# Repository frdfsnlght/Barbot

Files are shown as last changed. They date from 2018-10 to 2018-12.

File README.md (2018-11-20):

# Barbot
My Barbot project

This repository stores all the design artifacts for the project and is freely
available to anyone who wants to learn about my project.

## Why?

There are hundreds, if not thousands, of barbots made by makers all over the world.
It might be a right of passage for some, but for me, it was an interesting idea that
gave me an excuse to learn some new things.

I had the idea to build one of these things years ago with a friend. The main detraction
for me was that most barbot build I've seen are either too large or too slow, in my
opinion. If I was going to build one of these, it had to be small and convenient
enough to easily store when not in use, easy to clean after being used, and it couldn't
take forever to dispense a drink.
Those requirements are completely subjective but I eventually came up
with some numbers that would satisfy me. My goals were to be able to store the device
on an existing shelf in a spare room in my house and it had to be able to make me a
drink (e.g., a rum and coke) in under 10 seconds. The cleaning aspect is more difficult
to quantify but I didn't want to have to disassemble the device or do anything else
drastic to get it cleaned up.

## How?

In the spring of 2018 I revisited the idea of building a barbot when I found some
published builds using peristaltic pumps. I had never considered individual pumps
for each ingredient, but doing so solved some of the problems I felt other designs
suffered from. After investigating, I discovered peristaltic pumps generally come
in two forms, small and slow, or large and expensive. Neither was satisfactory, so
I started  considering making my own pumps. This eventually led to 3D printing,
something I had never really had a need of before. I started designing a
pump that could meet my needs and eventually bought a 3D printer and started
building a prototype. After a few iterations and lots of fiddling around, I came
up with a design that worked. You can find out more about the pump [here](3D).

Once I had the pump designed and tested, the possibility of building a complete
barbot became real. All I would need to do was the rest of the design and build.

## More to come...

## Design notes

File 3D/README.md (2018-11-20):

# 3D

These are SketchUp Make 2017 files for the most part.

## Enclosure

This file contains the model for the entire enclosure and most of the internal parts, except for the
pumps. Printable parts have been exported as STL to the STLs directory.

## Pump

This file contains all the parts for the planetary gear, peristaltic pump I designed. Every part except
the stepper motor can be printed and all parts have been exported to the STLs directory.

## Print Settings

All these parts were sliced with Slic3r Prusa Edition for an Original Prusa MK3 with a layer height of 0.15mm.

File            | Part                                                          | Material  | Infill            | Perimeters| Top/Bot   | Quantity
---             | ---                                                           | ---       | ---               | ---       | ---       | ---
Enclosure       | [Dispenser Head Part A](STLs/Dispenser%20Head%20Part%20A.stl) | PLA       | 40% Grid          | 2         | 7/5       | 1
Enclosure       | [Dispenser Head Part B](STLs/Dispenser%20Head%20Part%20B.stl) | PLA       | 20% Grid          | 2         | 7/5       | 1
Enclosure       | [Dispenser Head Part C](STLs/Dispenser%20Head%20Part%20C.stl) | PLA       | 40% Grid          | 2         | 7/5       | 1
Enclosure       | [Dispenser Head Part D](STLs/Dispenser%20Head%20Part%20D.stl) | PETG      | 40% Grid          | 2         | 7/5       | 1
Enclosure       | [Raspberry Pi Offset Bracket](STLs/Raspberry%20Pi%20Offset%20Bracket.stl) | PLA      | 20% Grid     | 2         | 7/5       | 4
Enclosure       | [Touch Screen Bracket](STLs/Touchscreen%20Bracket.stl)        | PETG      | 50% Grid          | 2         | 7/5       | 2
Enclosure       | [Drip Tray](STLs/Drip%20Tray.stl)                             | PETG      | 20% Grid          | 2         | 7/5       | 1
Enclosure       | [Drip Tray Cover](STLs/Drip%20Tray%20Cover.stl)               | PETG      | 15% Honeycomb     | 10        | 0/0       | 1
Enclosure       | [Speaker Grill](STLs/Speaker%20Grill.stl)                     | PETG      | 20% Honeycomb     | 8         | 0/0       | 2
Enclosure       | [Fan Grill](STLs/Fan%20Grill.stl)                             | PETG      | 15% Honeycomb     | 14        | 0/0       | 1
Enclosure       | [Tubing Bender](STLs/Tubing%20Bender.stl)                     | PETG      | 20% Grid          | 5         | 7/5       | 2
Pump            | [Sun Gear](STLs/Sun%20Gear.stl)                               | PLA       | 100% Rectilinear  | 5         | 7/5       | 32
Pump            | [Sun Roller](STLs/Sun%20Roller.stl)                           | PLA       | 50% Grid          | 5         | 7/5       | 16
Pump            | [Planet Gear](STLs/Planet%20Gear.stl)                         | PLA       | 100% Rectilinear  | 5         | 7/5       | 64
Pump            | [Planet Roller](STLs/Planet%20Roller.stl)                     | PLA       | 50% Grid          | 5         | 7/5       | 32
Pump            | [Clamp Block Left](STLs/Clamp%20Block%20Left.stl)             | PLA       | 20% Grid          | 2         | 7/5       | 16
Pump            | [Clamp Block Right](STLs/Clamp%20Block%20Right.stl)           | PLA       | 20% Grid          | 2         | 7/5       | 16
Pump            | [Motor Plate](STLs/Motor%20Plate.stl)                         | PLA       | 20% Grid          | 2         | 7/5       | 16
Pump            | [Ring Plate A](STLs/Ring%20Plate%20A.stl)                     | PLA       | 50% Grid          | 5         | 7/5       | 16
Pump            | [Ring Plate B](STLs/Ring%20Plate%20B.stl)                     | PLA       | 50% Grid          | 5         | 7/5       | 16
Pump            | [Body Plate A](STLs/Body%20Plate%20A.stl)                     | PLA       | 50% Grid          | 5         | 7/5       | 16
Pump            | [Body Plate B](STLs/Body%20Plate%20B.stl)                     | PLA       | 50% Grid          | 5         | 7/5       | 16

## Bill of Materials

This is a mostly complete list of every conceivable off-the-shelf part that will be required. You can find everything online,
but some of it can be found at a local, well stocked hardware store.
I've included links and approximate pricing where I could. Some of the online quantities are way more than you'll need.

### Hardware

Each item is linked to a McMaster-Carr product page and lists a price as of November 2018. I actually purchased much of this
from my local hardware store, but the larger quantity items were bought online. I've also substituted some hardware for other
pieces because I couldn't get some of the small quantities locally. For instance, rather than use 2.5mm screws to attach the
*Touchscreen Offset Bracket* to the back of the touchscreen, I tapped those holes to 3mm and used the same screws I used to
attach the Pi to the bracket. Use your best judgment.

Description                                                                                 | Quantity | Price
---                                                                                         | ---      | ---
[#8 x <sup>5</sup>/<sub>8</sub>" SS Phillips Oval Head Metal Screws](https://www.mcmaster.com/90315A467)          | 100 | $6.03
 *Side Panels*                                                                              |  16
 *Dispenser Panels*                                                                         |  16
 *Back*                                                                                     |   6
 *Controller*                                                                               |  14
 *Top Panel Brackets*                                                                       |   8
 *Pump Holder Brackets*                                                                     |   8
 *PCB Panel Brackets*                                                                       |   4
 *Power Supply Panel*                                                                       |   2
 *Relay Panel*                                                                              |   2
[#8 x 1" SS Phillips Round Head Metal Screws](https://www.mcmaster.com/92470A199)           | 100 | $8.13
 *LED Panel*                                                                                |   2
[#8 x <sup>5</sup>/<sub>8</sub>" SS Phillips Flat Head Metal Screws](https://www.mcmaster.com/90065A195)          | 100 | $5.50
 *Dispenser Panels*                                                                         |   2
 *Front*                                                                                    |   2
 *Pumps*                                                                                    |  32
 *Hinge Supports*                                                                           |   4
[#6 x <sup>5</sup>/<sub>8</sub>" SS Phillips Flat Head Metal Screws](https://www.mcmaster.com/90065A149)          | 100 | $3.89
 *Controller*                                                                               |   1
 *Hinges*                                                                                   |   4
[#6 x <sup>3</sup>/<sub>8</sub>" SS Phillips Flat Head Machine Screws](https://www.mcmaster.com/91771A146)        | 100 | $5.13
 *Hinges*                                                                                   |   4
[#4-40 x 5/8" Steel Phillips Flat Head Machine Screws](https://www.mcmaster.com/90273A112)  | 100 | $2.74
 *PCB Panel*                                                                                |  14
 *Relay Panel*                                                                              |   8
[#4-40 Steel Hex Nuts](https://www.mcmaster.com/90480A005)                                  | 100 | $0.89
 *PCB Panel*                                                                                |  14
 *Relay Panel*                                                                              |   8
[#8 x 1/4" x 1/4" Nylon Spacers](https://www.mcmaster.com/94639A293)                        | 100 | $8.75
 *PCBs*                                                                                     |  14
 *Relays*                                                                                   |   8
 *LED Panel*                                                                                |   4
[4mm x 35mm SS Socket Head Machine Screws](https://www.mcmaster.com/91292A131)              |  50 | $7.08
 *Fan*                                                                                      |   4
[4mm SS Hex Nuts](https://www.mcmaster.com/91828A231)                                       | 100 | $6.45
 *Fan*                                                                                      |   4
[3mm x 25mm SS Socket Head Machine Screws](https://www.mcmaster.com/91292A020)              | 100 | $6.87
 *Dispenser Head*                                                                           |   4
 *Pumps*                                                                                    |  80
[3mm x 20mm SS Socket Head Machine Screws](https://www.mcmaster.com/91292A123)              | 100 | $6.44
 *Dispenser Head*                                                                           |   1
 *Speakers*                                                                                 |   8
[3mm x 10mm SS Hex Drive Flat Head Machine Screws](https://www.mcmaster.com/92125A130)      | 100 | $5.81
 *Power Socket*                                                                             |   2
[3mm x 8mm SS Phillips Pan Head Machine Screws](https://www.mcmaster.com/92000A118)         | 100 | $4.33
 *Touchscreen Bracket*                                                                      |   4
 *PCB Panel*                                                                                |   4
[3mm x 8mm SS Hex Drive Flat Head Machine Screws](https://www.mcmaster.com/92125A128)       | 100 | $3.54
 *Power Supply Panel*                                                                       |   6
 *Pumps*                                                                                    |  64
[3mm x 12mm SS Hex Drive Button Head Machine Screws](https://www.mcmaster.com/92095A183)    | 100 | $4.00
 *Touchscreen Offset Bracket*                                                               |   4
[2.5mm x 12mm SS Hex Drive Button Head Machine Screws](https://www.mcmaster.com/92095A461)  |  25 | $9.57
 *Touchscreen Offset Bracket*                                                               |   4
[3mm SS Hex Nuts](https://www.mcmaster.com/91828A211)                                       | 100 | $5.55
 *Power Socket*                                                                             |   2
 *Pumps*                                                                                    |  80
 *Dispenser Head*                                                                           |   5
 *Speakers*                                                                                 |   8
 *Touchscreen Offset Bracket*                                                               |   4
[3mm SS Slim Hex Nuts](https://www.mcmaster.com/90710A030)                                  | 100 | $6.86
 *Pumps*                                                                                    |  32
[3mm x 5mm SS Flat Tip Set Screws](https://www.mcmaster.com/92605A099)                      |  50 | $5.72
 *Pumps*                                                                                    |  32
[<sup>1</sup>/<sub>8</sub>" x 1 <sup>3</sup>/<sub>8</sub>" OD O-Ring](https://www.mcmaster.com/9452K36)     | 100 | $8.81
 *Dispenser Head*                                                                           |   1
[3/4" x 9/16" Rubber Feet](https://www.mcmaster.com/8884T21)                                |  10 | $5.17
 *Bottom*                                                                                   |   4

### Electronics

Here's a list of all the electrical parts you'll need. Note, you'll also need the circuit boards that also part of this project,
as well as wire, a soldering iron, connectors, etc.

* Raspberry Pi 3 Model B (Amazon)
* 16GB Micro SD Card (Amazon)
* Teensy 3.2 (OSHPark with PCB order)
* Arduino Pro Mini
* Relays (eBay)
* Amplifier (Amazon)
* Speakers (Salvage)
* Stepper Drivers (AliExpress)
* 10 uF Capacitors (AliExpress)
* 1000 uF Capacitor (Amazon)
* Spade Solder Terminals (Amazon)
* Power Socket (eBay)
* Switch (Amazon)
* Stepper Motors (AliExpress)
* 80mm Fan (Salvage)
* IR Sensor (Amazon)
* 5V 12A Power Supply (Amazon)
* 24V 5A Power Supply (eBay)
* LEDs (eBay)
* Power Cord (Surplus)

### Other

Here's a few other important parts that didn't fit well in any other category.

* Funnel (Amazon)
* Hinges (Amazon)
* <sup>1</sup>/<sub>8</sub>" x 2' x 4' Acrylic Sheet, Black (Amazon)
* 4' x 4' x <sup>3</sup>/<sub>4</sub>" Birch Plywood (Surplus)
* Solid Birch Plank (Surplus)
* <sup>3</sup>/<sub>16</sub>" Brake Line (Amazon)
* 8mm/6mm Silicone Tubing (Amazon)
* 6mm/4mm Silicone Tubing (Amazon)

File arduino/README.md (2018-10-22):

# arduino
Firmware for Barbot's Arduino microcontroller.

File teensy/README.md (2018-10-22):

# teensy
Firmware for Barbot's Teensy microcontroller.

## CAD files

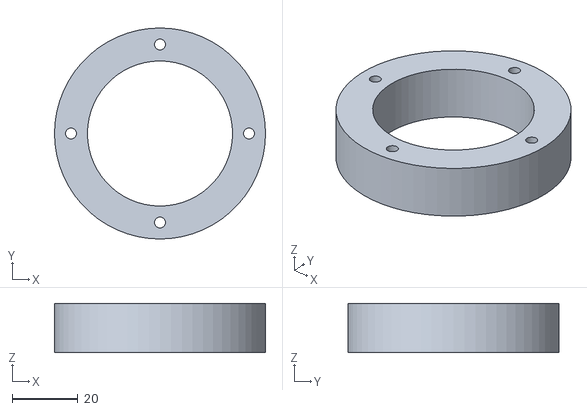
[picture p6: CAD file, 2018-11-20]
3D/STLs/Dispenser Head Part B.stl
64.0 x 64.0 x 15.0

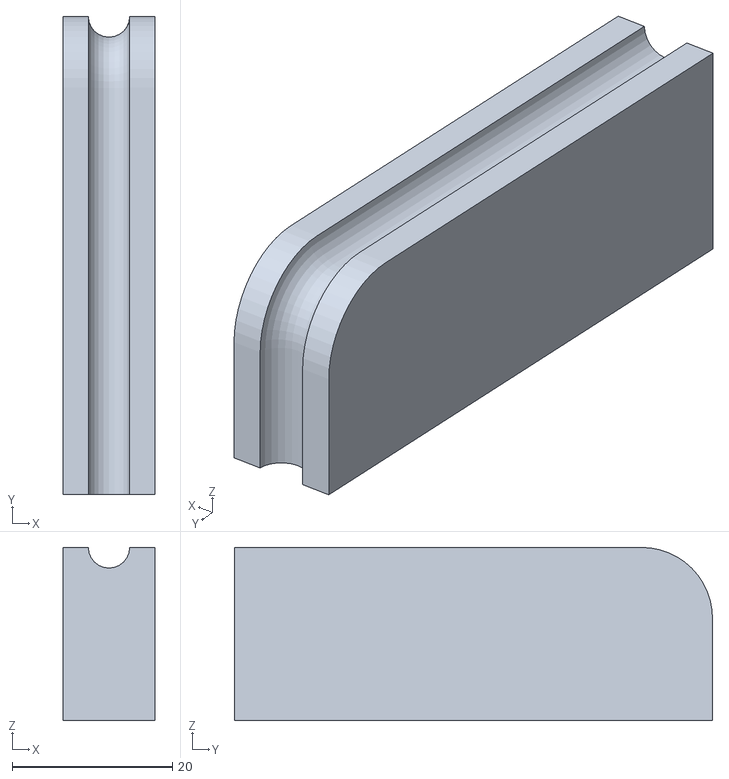
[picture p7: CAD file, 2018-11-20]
3D/STLs/Tubing Bender.stl
11.5 x 59.7 x 21.6

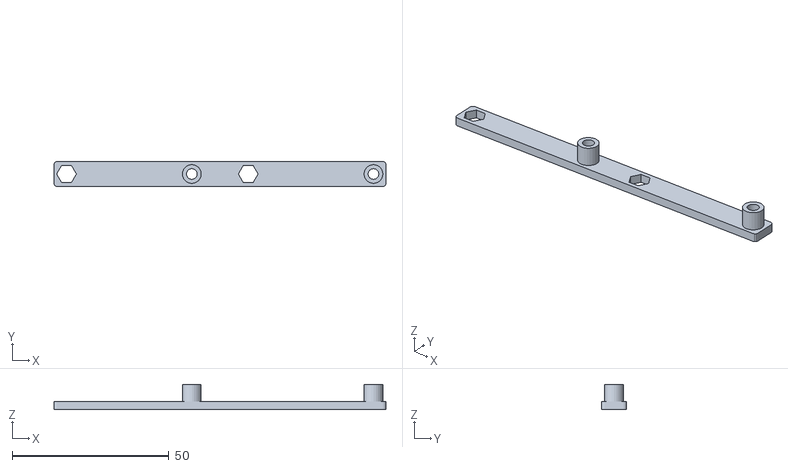
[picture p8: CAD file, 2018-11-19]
3D/STLs/Raspberry Pi Offset Bracket.stl
106.0 x 8.00 x 8.00

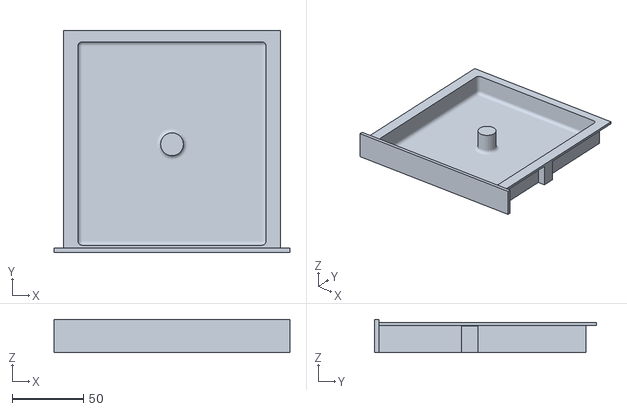
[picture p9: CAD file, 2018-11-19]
3D/STLs/Drip Tray.stl
165.1 x 155.2 x 23.3

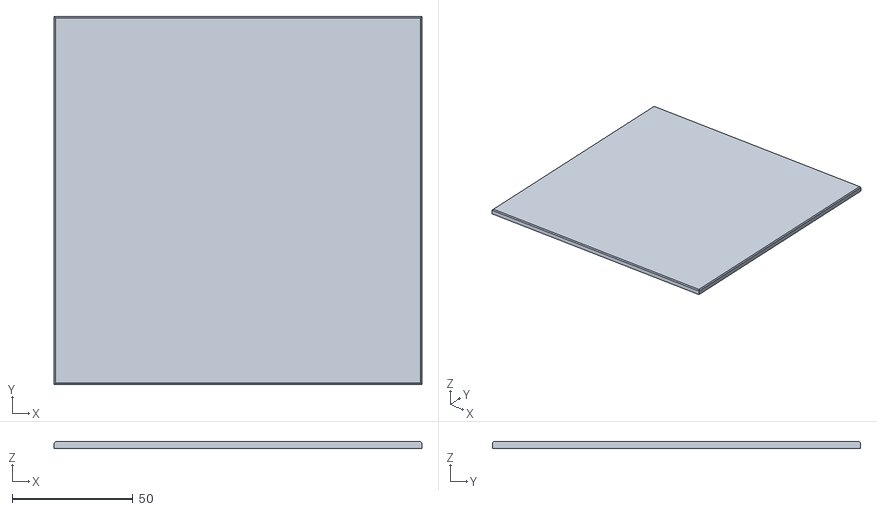
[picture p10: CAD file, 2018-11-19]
3D/STLs/Drip Tray Cover.stl
152.0 x 152.2 x 3.00

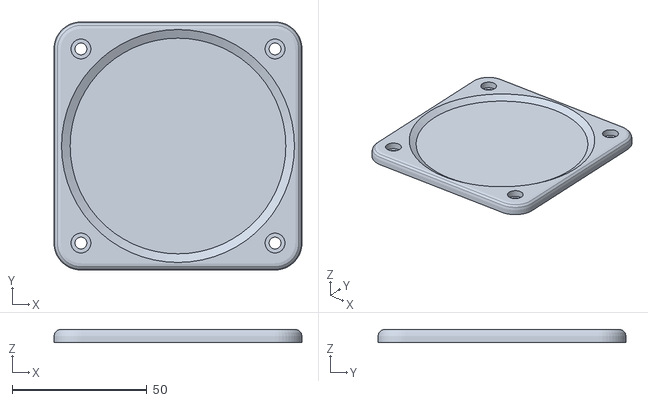
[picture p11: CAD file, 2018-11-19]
3D/STLs/Fan Grill.stl
92.0 x 92.0 x 5.00

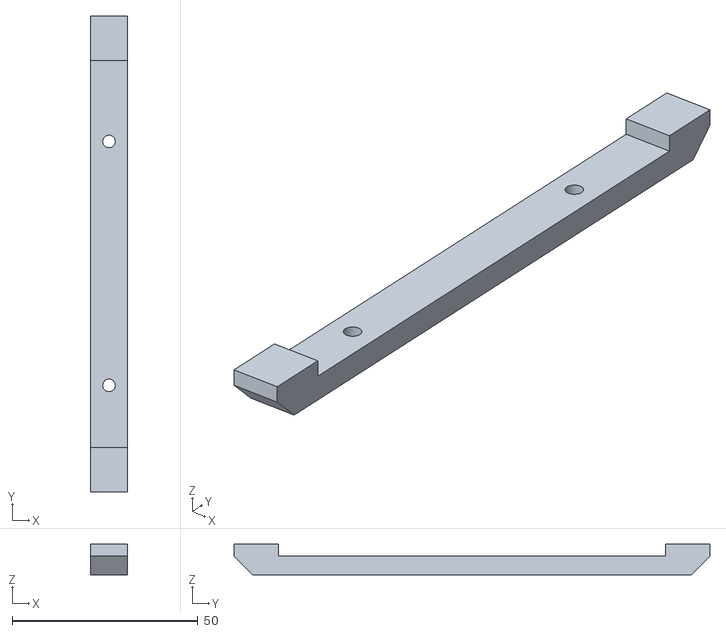
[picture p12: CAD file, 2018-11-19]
3D/STLs/Touchscreen Bracket.stl
10.0 x 128.1 x 8.24

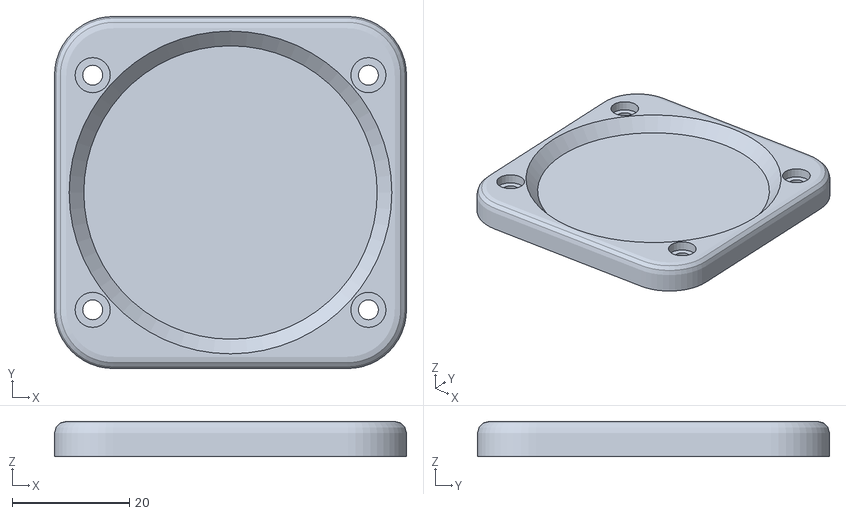
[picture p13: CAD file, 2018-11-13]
3D/STLs/Speaker Grill.stl
60.0 x 60.0 x 6.00

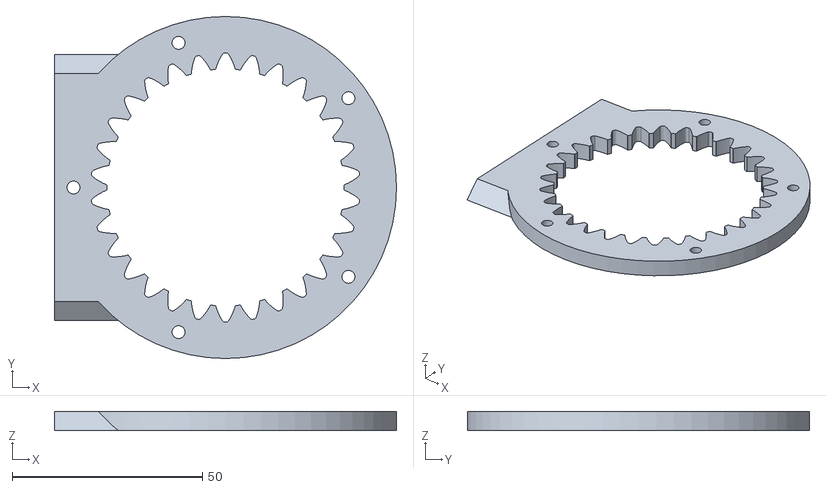
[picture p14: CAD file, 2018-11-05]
3D/STLs/Ring Plate A.stl
90.0 x 90.0 x 5.00

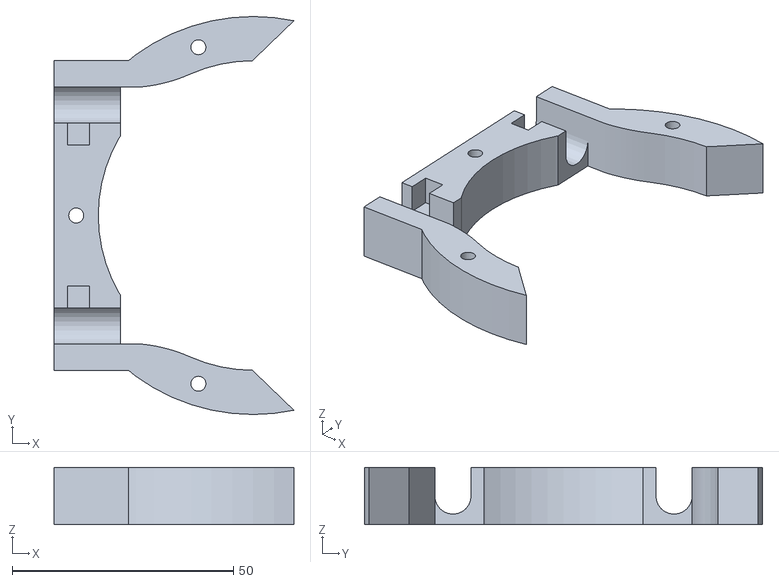
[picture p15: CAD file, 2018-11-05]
3D/STLs/Body Plate A.stl
54.2 x 90.0 x 13.0

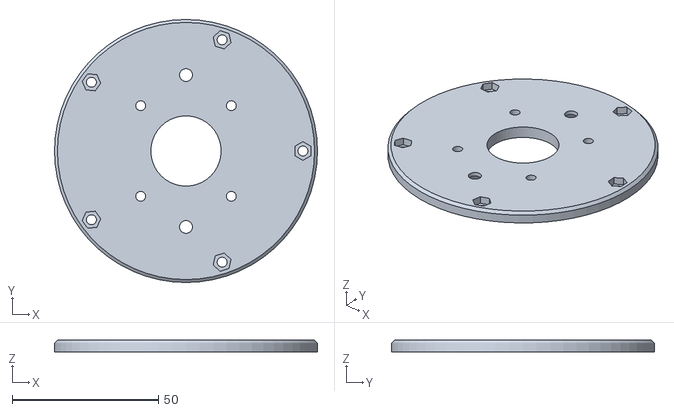
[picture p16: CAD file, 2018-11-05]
3D/STLs/Motor Plate.stl
90.0 x 90.0 x 4.00

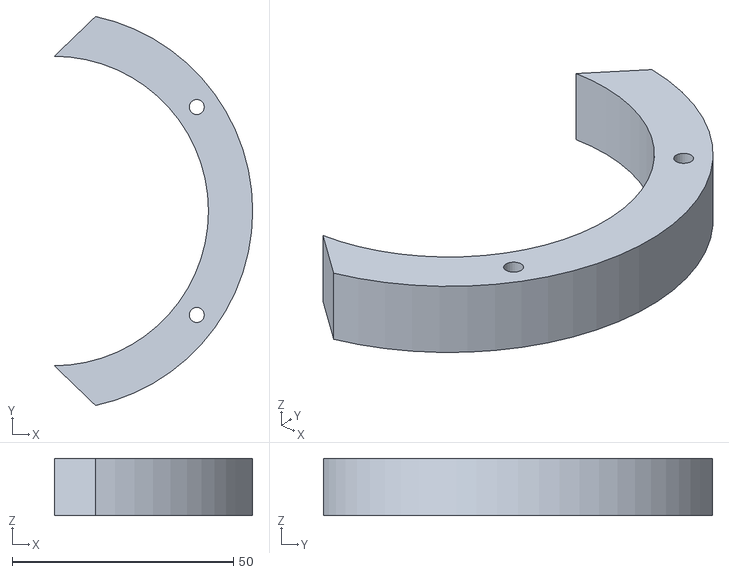
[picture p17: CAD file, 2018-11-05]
3D/STLs/Body Plate B.stl
44.9 x 88.0 x 13.0

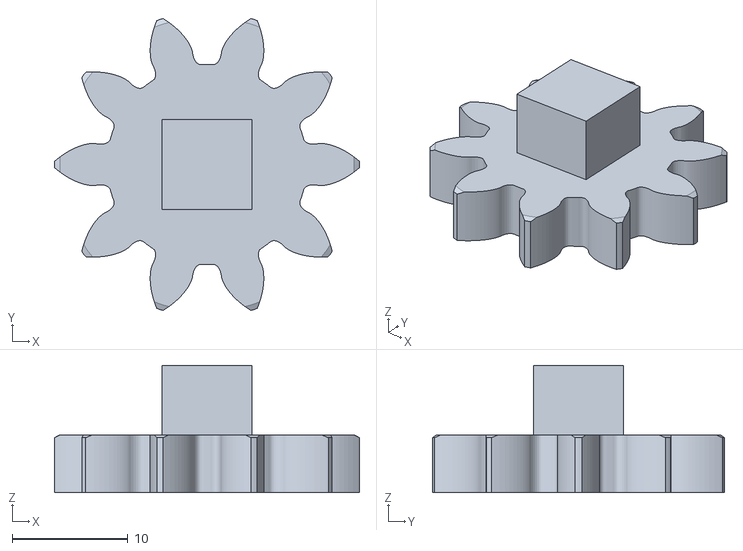
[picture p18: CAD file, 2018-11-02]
3D/STLs/Planet Gear.stl
26.4 x 25.3 x 11.0

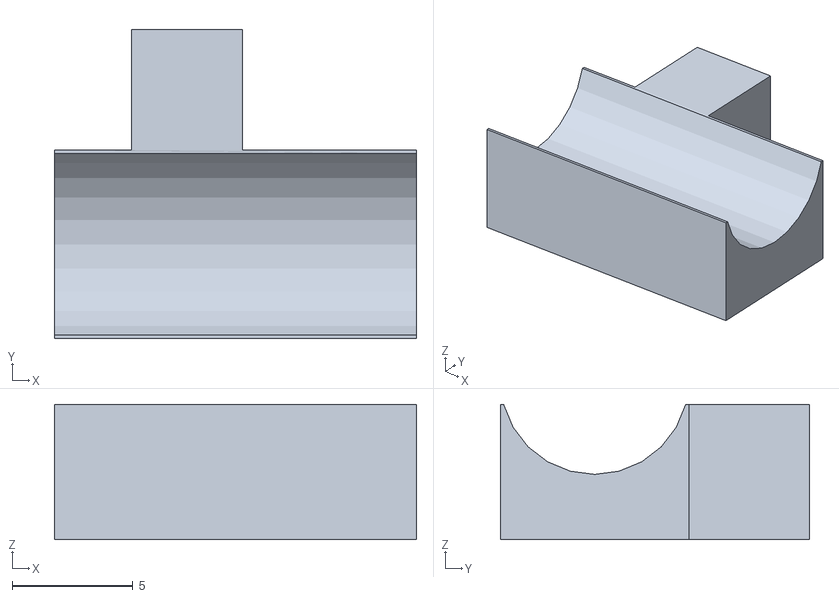
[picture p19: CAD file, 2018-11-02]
3D/STLs/Clamp Block Right.stl
15.0 x 12.8 x 5.60

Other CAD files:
3D/STLs/Ring Plate B.stl
3D/STLs/Planet Roller.stl
3D/STLs/Clamp Block Left.stl
3D/STLs/Dispenser Head Part C.stl
3D/Enclosure.skp
3D/Pump.skp
3D/STLs/Dispenser Head Part A.stl
3D/STLs/Dispenser Head Part D.stl
3D/STLs/Sun Gear.stl
3D/STLs/Sun Roller.stl

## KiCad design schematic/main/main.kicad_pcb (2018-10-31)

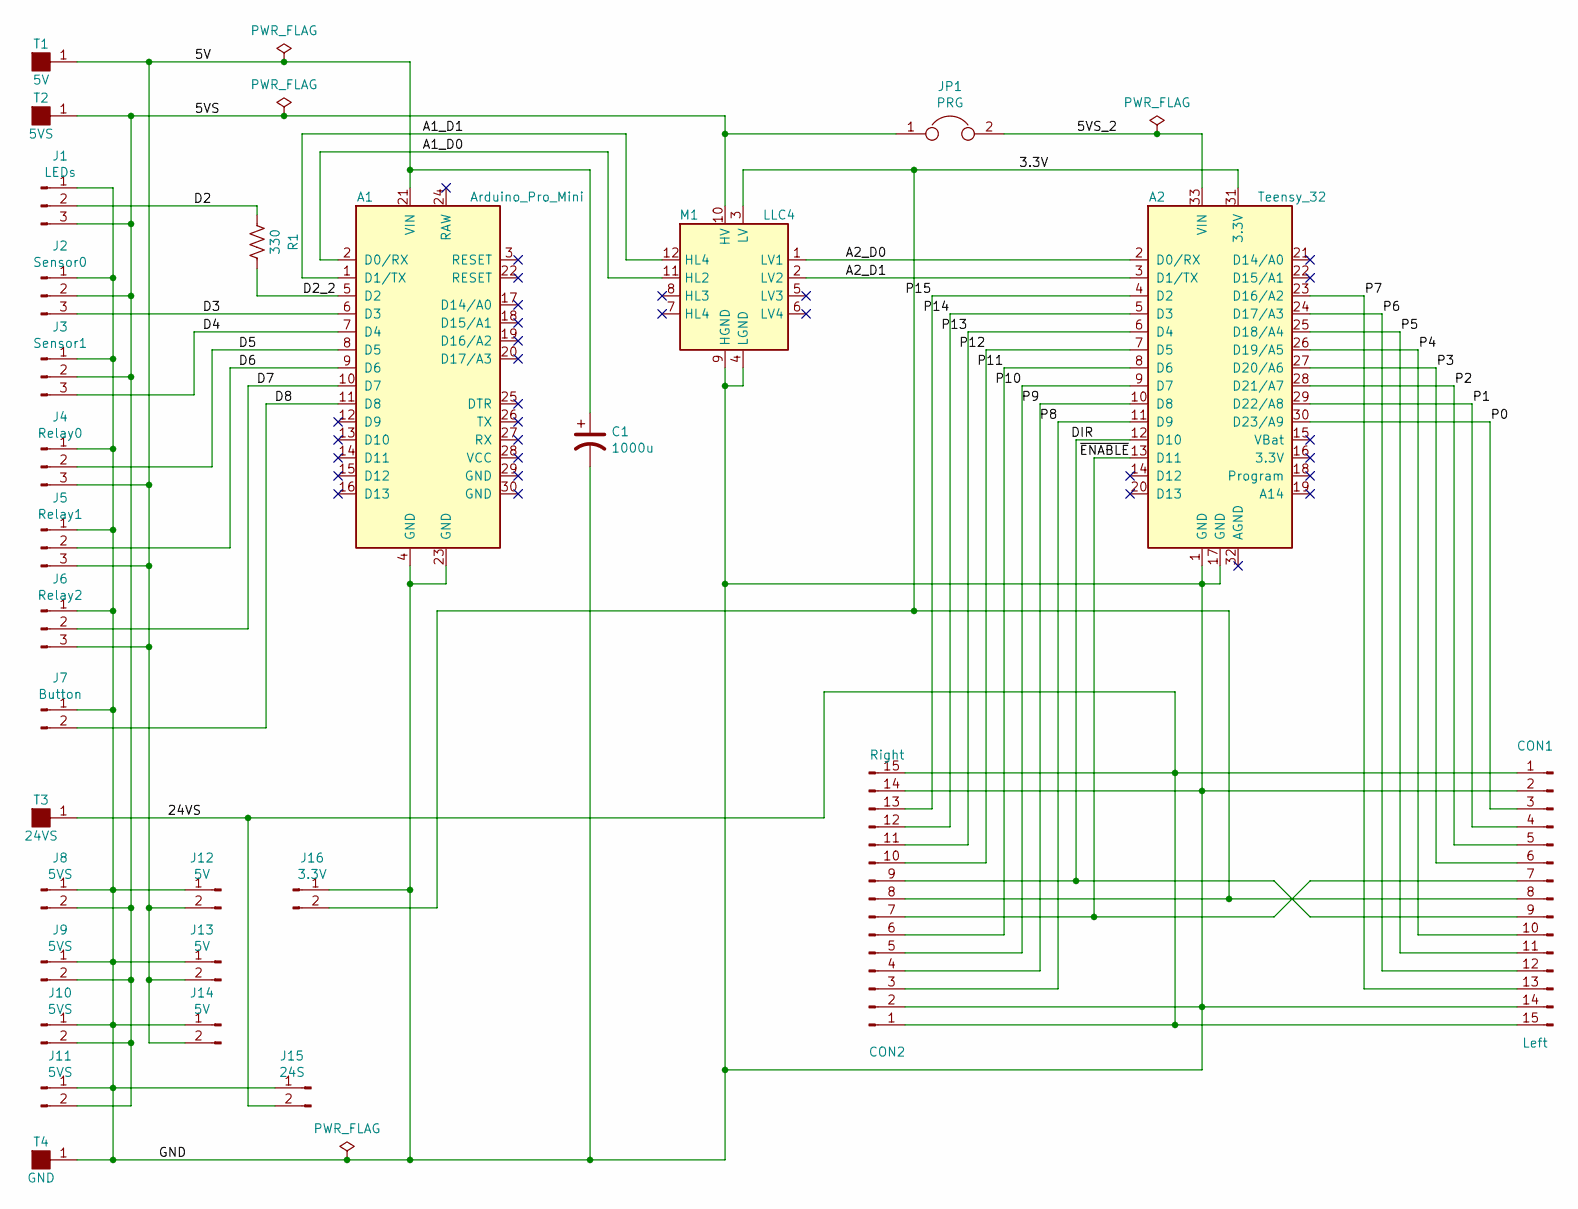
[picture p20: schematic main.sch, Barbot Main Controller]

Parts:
A1: Arduino_Pro_Mini; arduino_pro_mini
A2: Teensy_32; teensy_32
C1: 1000u; CP_Radial_D10.0mm_P5.00mm
CON1: Left; Pin_Header_Angled_1x15_Pitch2.54mm
CON2: Right; Pin_Header_Angled_1x15_Pitch2.54mm
J1: LEDs; Pin_Header_Straight_1x03_Pitch2.54mm
J2: Sensor0; Pin_Header_Straight_1x03_Pitch2.54mm
J3: Sensor1; Pin_Header_Straight_1x03_Pitch2.54mm
J4: Relay0; Pin_Header_Straight_1x03_Pitch2.54mm
J5: Relay1; Pin_Header_Straight_1x03_Pitch2.54mm
J6: Relay2; Pin_Header_Straight_1x03_Pitch2.54mm
J7: Button; Pin_Header_Straight_1x02_Pitch2.54mm
J8, J9, J10, J11: 5VS; Pin_Header_Straight_1x02_Pitch2.54mm
J12, J13, J14: 5V; Pin_Header_Straight_1x02_Pitch2.54mm
J15: 24S; Pin_Header_Straight_1x02_Pitch2.54mm
J16: 3.3V; Pin_Header_Straight_1x02_Pitch2.54mm
JP1: PRG; Pin_Header_Straight_1x02_Pitch2.54mm
M1: LLC4
R1: 330; R_Axial_DIN0207_L6.3mm_D2.5mm_P2.54mm_Vertical
T1: 5V; Spade_Terminal_1_4
T2: 5VS; Spade_Terminal_1_4
T3: 24VS; Spade_Terminal_1_4
T4: GND; Spade_Terminal_1_4

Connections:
/3.3V: A2.31 (3.3V), CON1.8, CON2.8, J16.2, M1.3 (LV)
/5V: A1.21 (VIN), C1.1, J4.3, J5.3, J6.3, J12.2, J13.2, J14.2, T1.1
/5VS: J1.3, J2.2, J3.2, J8.2, J9.2, J10.2, J11.2, JP1.1, M1.10 (HV), T2.1
/5VS_2: A2.33 (VIN), JP1.2
/24VS: CON1.1, CON1.15, CON2.1, CON2.15, J15.2, T3.1
/A1_D0: A1.2 (D0/RX), M1.11 (HL2)
/A1_D1: A1.1 (D1/TX), M1.12 (HL4)
/A2_D0: A2.2 (D0/RX), M1.1 (LV1)
/A2_D1: A2.3 (D1/TX), M1.2 (LV2)
/D2: J1.2, R1.1
/D2_2: A1.5 (D2), R1.2
/D3: A1.6 (D3), J2.3
/D4: A1.7 (D4), J3.3
/D5: A1.8 (D5), J4.2
/D6: A1.9 (D6), J5.2
/D7: A1.10 (D7), J6.2
/D8: A1.11 (D8), J7.2
/DIR: A2.12 (D10), CON1.9, CON2.9
/GND: A1.4 (GND), A1.23 (GND), A2.1 (GND), A2.17 (GND), C1.2, CON1.2, CON1.14, CON2.2, CON2.14, J1.1, J2.1, J3.1, J4.1, J5.1, J6.1, J7.1, J8.1, J9.1, J10.1, J11.1, J12.1, J13.1, J14.1, J15.1, J16.1, M1.4 (LGND), M1.9 (HGND), T4.1
/P0: A2.30 (D23/A9), CON1.3
/P1: A2.29 (D22/A8), CON1.4
/P2: A2.28 (D21/A7), CON1.5
/P3: A2.27 (D20/A6), CON1.6
/P4: A2.26 (D19/A5), CON1.10
/P5: A2.25 (D18/A4), CON1.11
/P6: A2.24 (D17/A3), CON1.12
/P7: A2.23 (D16/A2), CON1.13
/P8: A2.11 (D9), CON2.3
/P9: A2.10 (D8), CON2.4
/P10: A2.9 (D7), CON2.5
/P11: A2.8 (D6), CON2.6
/P12: A2.7 (D5), CON2.10
/P13: A2.6 (D4), CON2.11
/P14: A2.5 (D3), CON2.12
/P15: A2.4 (D2), CON2.13
/~ENABLE: A2.13 (D11), CON1.7, CON2.7

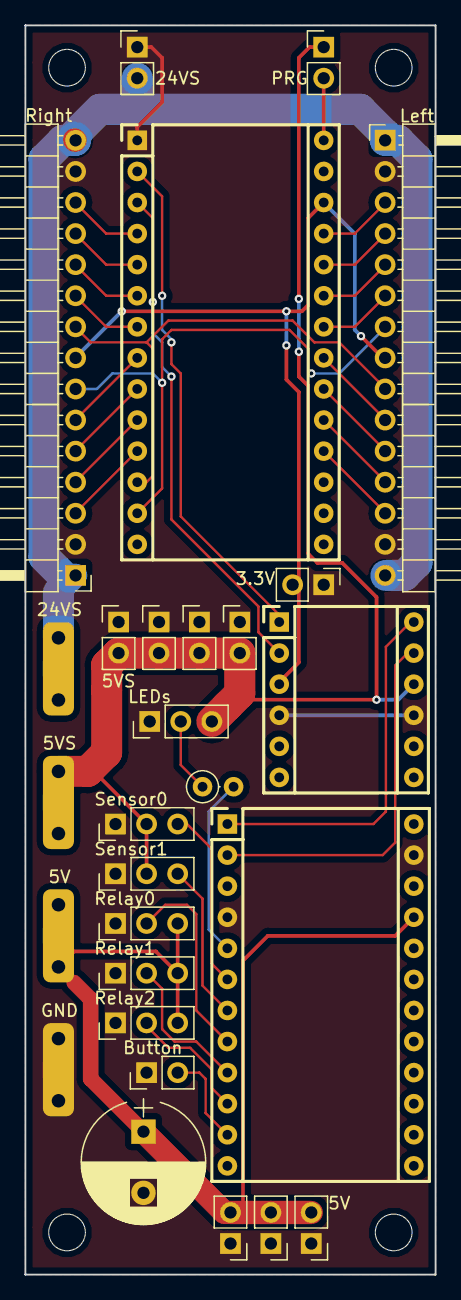
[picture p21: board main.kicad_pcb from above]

Board: 2 copper layers, 33.5 x 102.1 mm, 28 parts (0 on the bottom side), 36 nets.

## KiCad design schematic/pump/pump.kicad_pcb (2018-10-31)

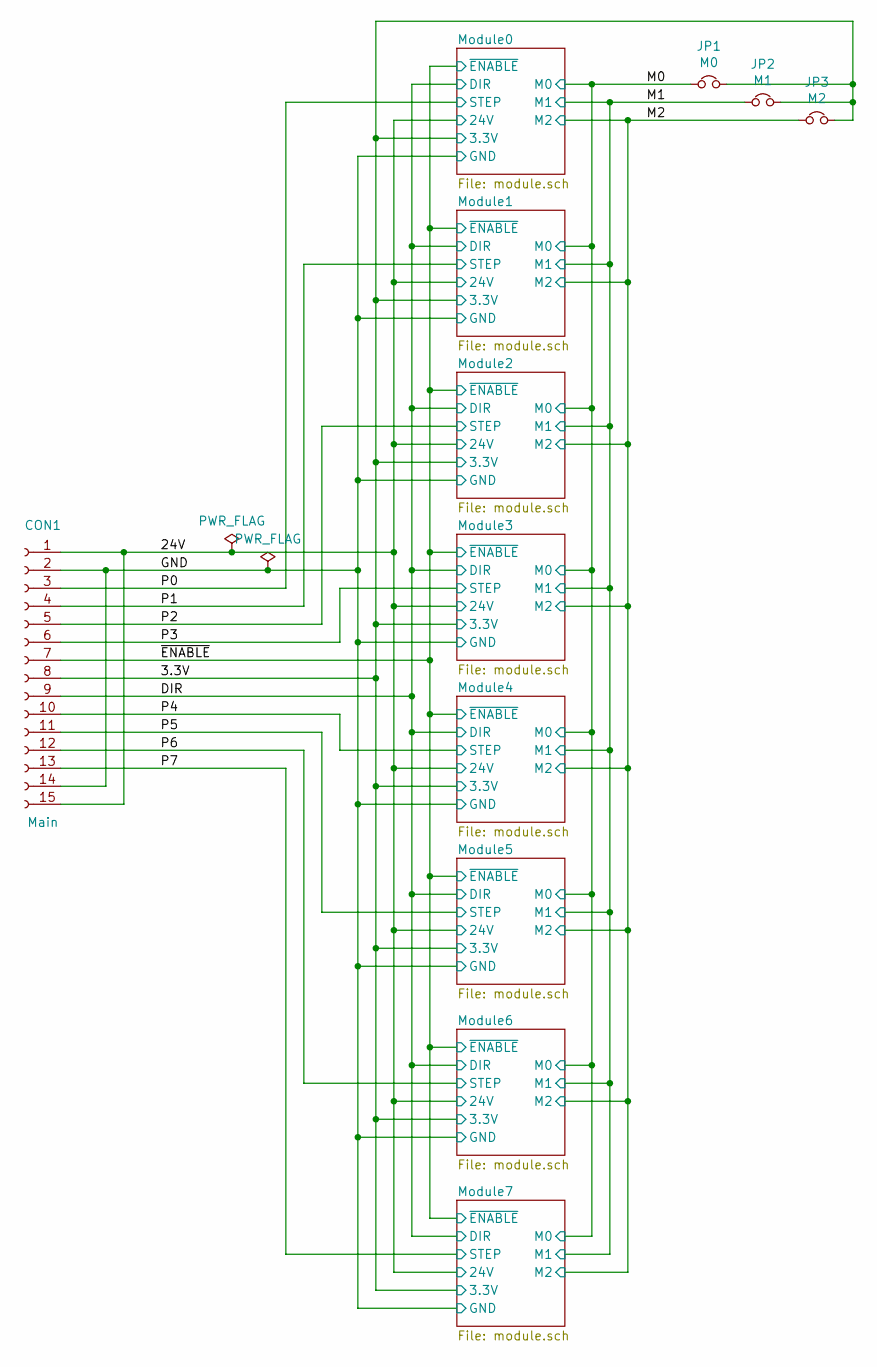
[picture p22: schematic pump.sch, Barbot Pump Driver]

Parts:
CON1: Main; Socket_Strip_Angled_1x15_Pitch2.54mm
JP1: M0; Pin_Header_Straight_2x01_Pitch2.54mm
JP2: M1; Pin_Header_Straight_2x01_Pitch2.54mm
JP3: M2; Pin_Header_Straight_2x01_Pitch2.54mm

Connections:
/3.3V: CON1.8, JP1.2, JP2.2, JP3.2; also elsewhere on the board
/24V: CON1.1, CON1.15; also elsewhere on the board
/DIR: CON1.9; also elsewhere on the board
/GND: CON1.2, CON1.14; also elsewhere on the board
/M0: JP1.1; also elsewhere on the board
/M1: JP2.1; also elsewhere on the board
/M2: JP3.1; also elsewhere on the board
/P0: CON1.3; also elsewhere on the board
/P1: CON1.4; also elsewhere on the board
/P2: CON1.5; also elsewhere on the board
/P3: CON1.6; also elsewhere on the board
/P4: CON1.10; also elsewhere on the board
/P5: CON1.11; also elsewhere on the board
/P6: CON1.12; also elsewhere on the board
/P7: CON1.13; also elsewhere on the board
/~ENABLE: CON1.7; also elsewhere on the board

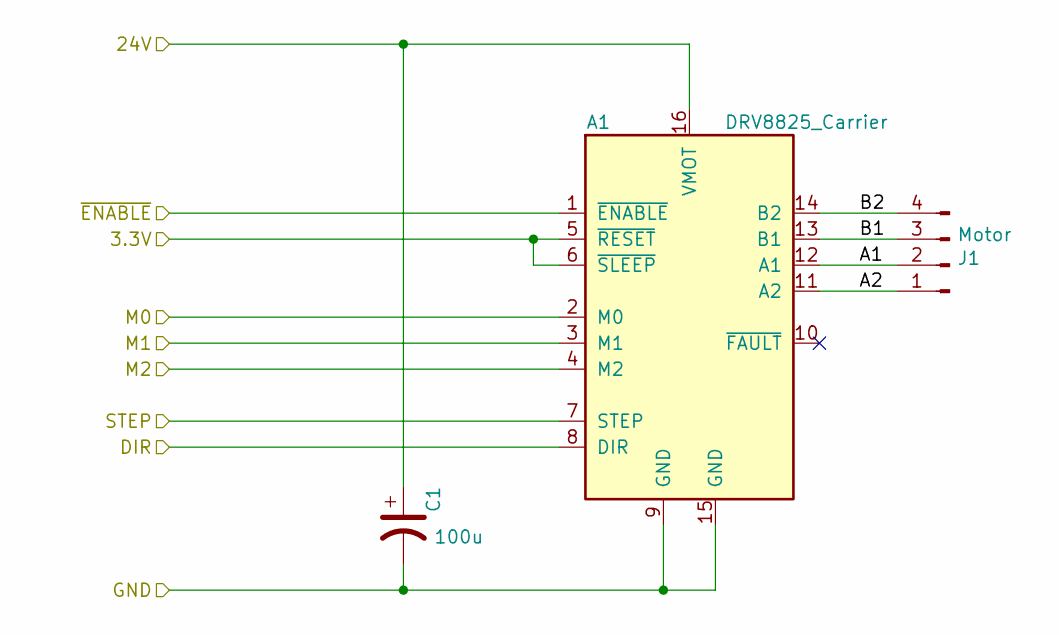
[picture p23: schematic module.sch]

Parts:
A1: DRV8825_Carrier; Pololu_Breakout-16_15.2x20.3mm
C1: 100u; CP_Radial_D6.3mm_P2.50mm
J1: Motor; Pin_Header_Straight_1x04_Pitch2.54mm

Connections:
/3.3V: A1.5 (~RESET), A1.6 (~SLEEP); also elsewhere on the board
/24V: A1.16 (VMOT), C1.1; also elsewhere on the board
/DIR: A1.8 (DIR); also elsewhere on the board
/GND: A1.9 (GND), A1.15 (GND), C1.2; also elsewhere on the board
/M0: A1.2 (M0); also elsewhere on the board
/M1: A1.3 (M1); also elsewhere on the board
/M2: A1.4 (M2); also elsewhere on the board
/Module1/A1: A1.12 (A1), J1.2
/Module1/A2: A1.11 (A2), J1.1
/Module1/B1: A1.13 (B1), J1.3
/Module1/B2: A1.14 (B2), J1.4
/P1: A1.7 (STEP); also elsewhere on the board
/~ENABLE: A1.1 (~ENABLE); also elsewhere on the board

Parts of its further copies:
A0, A2, A3, A4, A5, A6, A7: DRV8825_Carrier; Pololu_Breakout-16_15.2x20.3mm
C0, C2, C3, C4, C5, C6, C7: 100u; CP_Radial_D6.3mm_P2.50mm
J0, J2, J3, J4, J5, J6, J7: Motor; Pin_Header_Straight_1x04_Pitch2.54mm

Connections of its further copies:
/3.3V: A0.5 (~RESET), A0.6 (~SLEEP), A2.5 (~RESET), A2.6 (~SLEEP), A3.5 (~RESET), A3.6 (~SLEEP), A4.5 (~RESET), A4.6 (~SLEEP), A5.5 (~RESET), A5.6 (~SLEEP), A6.5 (~RESET), A6.6 (~SLEEP), A7.5 (~RESET), A7.6 (~SLEEP); also elsewhere on the board
/24V: A0.16 (VMOT), A2.16 (VMOT), A3.16 (VMOT), A4.16 (VMOT), A5.16 (VMOT), A6.16 (VMOT), A7.16 (VMOT), C0.1, C2.1, C3.1, C4.1, C5.1, C6.1, C7.1; also elsewhere on the board
/DIR: A0.8 (DIR), A2.8 (DIR), A3.8 (DIR), A4.8 (DIR), A5.8 (DIR), A6.8 (DIR), A7.8 (DIR); also elsewhere on the board
/GND: A0.9 (GND), A0.15 (GND), A2.9 (GND), A2.15 (GND), A3.9 (GND), A3.15 (GND), A4.9 (GND), A4.15 (GND), A5.9 (GND), A5.15 (GND), A6.9 (GND), A6.15 (GND), A7.9 (GND), A7.15 (GND), C0.2, C2.2, C3.2, C4.2, C5.2, C6.2, C7.2; also elsewhere on the board
/M0: A0.2 (M0), A2.2 (M0), A3.2 (M0), A4.2 (M0), A5.2 (M0), A6.2 (M0), A7.2 (M0); also elsewhere on the board
/M1: A0.3 (M1), A2.3 (M1), A3.3 (M1), A4.3 (M1), A5.3 (M1), A6.3 (M1), A7.3 (M1); also elsewhere on the board
/M2: A0.4 (M2), A2.4 (M2), A3.4 (M2), A4.4 (M2), A5.4 (M2), A6.4 (M2), A7.4 (M2); also elsewhere on the board
/Module0/A1: A0.12 (A1), J0.2
/Module0/A2: A0.11 (A2), J0.1
/Module0/B1: A0.13 (B1), J0.3
/Module0/B2: A0.14 (B2), J0.4
/Module2/A1: A2.12 (A1), J2.2
/Module2/A2: A2.11 (A2), J2.1
/Module2/B1: A2.13 (B1), J2.3
/Module2/B2: A2.14 (B2), J2.4
/Module3/A1: A3.12 (A1), J3.2
/Module3/A2: A3.11 (A2), J3.1
/Module3/B1: A3.13 (B1), J3.3
/Module3/B2: A3.14 (B2), J3.4
/Module4/A1: A4.12 (A1), J4.2
/Module4/A2: A4.11 (A2), J4.1
/Module4/B1: A4.13 (B1), J4.3
/Module4/B2: A4.14 (B2), J4.4
/Module5/A1: A5.12 (A1), J5.2
/Module5/A2: A5.11 (A2), J5.1
/Module5/B1: A5.13 (B1), J5.3
/Module5/B2: A5.14 (B2), J5.4
/Module6/A1: A6.12 (A1), J6.2
/Module6/A2: A6.11 (A2), J6.1
/Module6/B1: A6.13 (B1), J6.3
/Module6/B2: A6.14 (B2), J6.4
/Module7/A1: A7.12 (A1), J7.2
/Module7/A2: A7.11 (A2), J7.1
/Module7/B1: A7.13 (B1), J7.3
/Module7/B2: A7.14 (B2), J7.4
/P0: A0.7 (STEP); also elsewhere on the board
/P2: A2.7 (STEP); also elsewhere on the board
/P3: A3.7 (STEP); also elsewhere on the board
/P4: A4.7 (STEP); also elsewhere on the board
/P5: A5.7 (STEP); also elsewhere on the board
/P6: A6.7 (STEP); also elsewhere on the board
/P7: A7.7 (STEP); also elsewhere on the board
/~ENABLE: A0.1 (~ENABLE), A2.1 (~ENABLE), A3.1 (~ENABLE), A4.1 (~ENABLE), A5.1 (~ENABLE), A6.1 (~ENABLE), A7.1 (~ENABLE); also elsewhere on the board

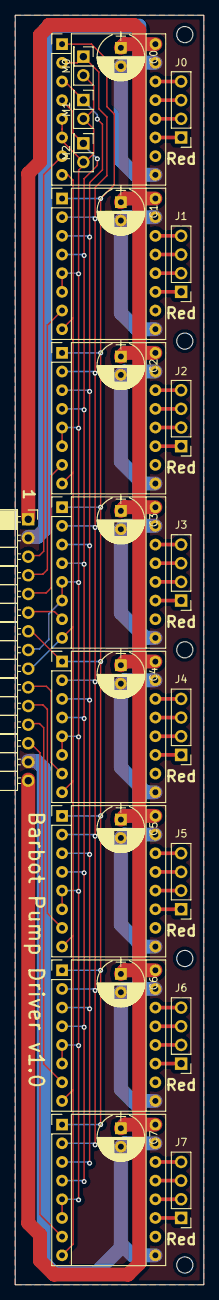
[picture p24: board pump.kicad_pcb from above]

Board: 2 copper layers, 25.7 x 172.7 mm, 28 parts (0 on the bottom side), 48 nets.

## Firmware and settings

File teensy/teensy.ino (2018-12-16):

/*
Copyright 2018 Thomas A. Bennedum

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
THE SOFTWARE IS PROVIDED "AS IS", WITHOUT WARRANTY OF ANY KIND, EXPRESS OR
IMPLIED, INCLUDING BUT NOT LIMITED TO THE WARRANTIES OF MERCHANTABILITY,
FITNESS FOR A PARTICULAR PURPOSE AND NONINFRINGEMENT. IN NO EVENT SHALL
THE AUTHORS OR COPYRIGHT HOLDERS BE LIABLE FOR ANY CLAIM, DAMAGES OR OTHER
LIABILITY, WHETHER IN AN ACTION OF CONTRACT, TORT OR OTHERWISE, ARISING
FROM, OUT OF OR IN CONNECTION WITH THE SOFTWARE OR THE USE OR OTHER DEALINGS
IN THE SOFTWARE.
*/

/*
    https://github.com/frdfsnlght/TeensyStep
*/

#include <Arduino.h>
#include <avr_functions.h>
#include <StepControl.h>

constexpr int PIN_LED                   = LED_BUILTIN;
constexpr int PIN_ENABLE                = 11;
constexpr int PIN_DIR                   = 10;
constexpr int SERIAL1_PIN_RX            = 0;
constexpr int SERIAL1_PIN_TX            = 1;

constexpr int PUMPS                     = 16;

constexpr int PUMP_MAX_SPEED            = 500000;
constexpr int PUMP_MIN_SPEED            = 40;
constexpr int PUMP_DEF_SPEED            = 12000;
constexpr int PUMP_MAX_ACCEL            = 500000;
constexpr int PUMP_MIN_ACCEL            = 1;
constexpr int PUMP_DEF_ACCEL            = 7500;

constexpr int PUMP_CONTROLLERS          = 4;

constexpr int INPUT_BUFFERS             = 2;
constexpr int INPUT_BUFFER_LENGTH       = 50;
constexpr int BUF_SERIAL                = 0;
constexpr int BUF_SERIAL1               = 1;

constexpr unsigned long LED_TOGGLE_INTERVAL = 500;

constexpr int ERR_OK                    = 0;
constexpr int ERR_PUMPS_ARE_RUNNING     = 1;

constexpr uint32_t SERIAL_SPEEDS[]      = {115200, 58824, 38400, 19200, 9600};
constexpr int NUM_SERIAL_SPEEDS         = sizeof(SERIAL_SPEEDS) / sizeof(uint32_t);
constexpr unsigned long SERIAL_SPEED_CHECK_INTERVAL = 2000;
constexpr int PING_TIMEOUT              = 3000;

constexpr int CHECKSUM_RETRIES          = 3;


typedef struct {
    char data[INPUT_BUFFER_LENGTH + 1];
    uint16_t length;
} inputBuffer_t;
    
inputBuffer_t inputBuffers[INPUT_BUFFERS];
int ch;

Stepper pump0(23, PIN_DIR);
Stepper pump1(22, PIN_DIR);
Stepper pump2(21, PIN_DIR);
Stepper pump3(20, PIN_DIR);
Stepper pump4(19, PIN_DIR);
Stepper pump5(18, PIN_DIR);
Stepper pump6(17, PIN_DIR);
Stepper pump7(16, PIN_DIR);

Stepper pump8(2, PIN_DIR);
Stepper pump9(3, PIN_DIR);
Stepper pump10(4, PIN_DIR);
Stepper pump11(5, PIN_DIR);
Stepper pump12(6, PIN_DIR);
Stepper pump13(7, PIN_DIR);
Stepper pump14(8, PIN_DIR);
Stepper pump15(9, PIN_DIR);

Stepper* allPumps[] = {&pump0, &pump1, &pump2, &pump3, &pump4, &pump5, &pump6, &pump7,
                       &pump8, &pump9, &pump10, &pump11, &pump12, &pump13, &pump14, &pump15};

StepControl<> pumpCtrl0;
StepControl<> pumpCtrl1;
StepControl<> pumpCtrl2;
StepControl<> pumpCtrl3;
StepControl<>* allPumpControllers[] = {&pumpCtrl0, &pumpCtrl1, &pumpCtrl2, &pumpCtrl3};

StepControl<>* pumpControllers[PUMPS];
int pumpDir = 0;
int pumpSpeed = PUMP_DEF_SPEED;
unsigned pumpAccel = PUMP_DEF_ACCEL;
bool pumpsEnabled = false;
bool pumpsEnabledOverride = false;
bool pumpsFlushing = false;

uint32_t lastSerialSpeedCheck = 0;
uint32_t serialSpeed = 0;
bool commEnabled = true;

bool ledOn = false;
uint32_t lastLEDToggle = 0;

uint8_t checksumRetries = 0;
char lastSerial1Command[INPUT_BUFFER_LENGTH + 1];


void setup() {
    Serial.begin(115200); // speed is ignored
    
    pinMode(PIN_LED, OUTPUT);
    pinMode(PIN_ENABLE, OUTPUT);
    turnOffLED();
    disablePumps();
    
    sendMessage("Barbot-Teensy ready");
}

void loop() {
    loopSerial();
    loopSerial1();
    loopPumps();
    loopLED();
}

void loopSerial() {
    while (Serial.available()) {
        ch = Serial.read();
        if ((ch == '\r') || (ch == '\n')) {
            if (inputBuffers[BUF_SERIAL].length) {
                processCommand();
            }
            resetInputBuffer(BUF_SERIAL);
        } else if (ch == 8) {
            if (inputBuffers[BUF_SERIAL].length) {
                inputBuffers[BUF_SERIAL].length--;
                inputBuffers[BUF_SERIAL].data[inputBuffers[BUF_SERIAL].length] = '\0';
            }
        } else if (ch == 27) {
            if (inputBuffers[BUF_SERIAL].length) {
                resetInputBuffer(BUF_SERIAL);
                send("CANCELED\n");
            }
        } else if ((ch >= 32) && (ch <= 126)) {
            if (inputBuffers[BUF_SERIAL].length == INPUT_BUFFER_LENGTH) {
                resetInputBuffer(BUF_SERIAL);
                sendError("overflow");
                return;
            }
            appendInputBuffer(BUF_SERIAL, ch);
        }
    }
}

void loopSerial1() {

    if (! commEnabled) return;
    
    if (! serialSpeed) {
        if ((millis() - lastSerialSpeedCheck) > SERIAL_SPEED_CHECK_INTERVAL) {
            lastSerialSpeedCheck = millis();
            detectSerial1Speed();
        }
    }
    
    while (serialSpeed && Serial1.available()) {
        ch = Serial1.read();
        if ((ch == '\r') || (ch == '\n')) {
            if (inputBuffers[BUF_SERIAL1].length) {
                if ((strcmp(inputBuffers[BUF_SERIAL1].data, "!CHK") == 0) && (checksumRetries < CHECKSUM_RETRIES)) {
                    checksumRetries++;
                    sendMessage("retry");
                    Serial1.println(lastSerial1Command);
                } else {
                    send(inputBuffers[BUF_SERIAL1].data);
                    sendChar('\n');
                }
            }
            resetInputBuffer(BUF_SERIAL1);
        } else {
            appendInputBuffer(BUF_SERIAL1, ch);
        }
    }
}

void loopPumps() {
    bool running = false;
    for (byte i = 0; i < PUMPS; i++) {
        if (pumpControllers[i]) {
            if (! pumpControllers[i]->isRunning()) {
                pumpControllers[i] = NULL;
                sendPumpStopped(i);
            } else {
                running = true;
            }
        }
    }
    if (running) {
        delay(1);
    } else {
        if (pumpsFlushing)
            pumpsFlushing = false;
        if (pumpsEnabled and (! pumpsEnabledOverride)) {
            disablePumps();
            pumpDir = 0;
        }
    }
}

void loopLED() {
    if (! pumpsEnabled && ((millis() - lastLEDToggle) >= LED_TOGGLE_INTERVAL)) {
        lastLEDToggle = millis();
        toggleLED();
    }
}

bool detectSerial1Speed() {
    for (int i = 0; i < NUM_SERIAL_SPEEDS; i++) {
        send("# trying ");
        sendInt(SERIAL_SPEEDS[i]);
        sendChar('\n');
        
        Serial1.begin(SERIAL_SPEEDS[i], SERIAL_8N1);
        if (ping()) {
            serialSpeed = SERIAL_SPEEDS[i];
            send("# detected ");
            sendInt(serialSpeed);
            sendChar('\n');
            return true;
        }
    }
    serialSpeed = 0;
    return false;
}

bool ping() {
    while (Serial1.available())
        Serial1.read();
    Serial1.print((char)24);
    Serial1.print((char)24);
    Serial1.print((char)24);
    Serial1.print((char)24);
    Serial1.println("PING");
    unsigned long time = millis();
    while ((millis() - time) < PING_TIMEOUT) {
        while (Serial1.available()) {
            ch = Serial1.read();
            send("# received ");
            sendInt(ch);
            sendChar('\n');
            if ((ch == '\r') || (ch == '\n')) {
                if (inputBuffers[BUF_SERIAL1].length && 
                    strcmp(inputBuffers[BUF_SERIAL1].data, "PONG") == 0) {
                    resetInputBuffer(BUF_SERIAL1);
                    return true;
                }
                resetInputBuffer(BUF_SERIAL1);
            } else if (ch == 24) {
                    resetInputBuffer(BUF_SERIAL1);
            } else if (inputBuffers[BUF_SERIAL1].length == 0) {
                if (ch == 'P') {
                    appendInputBuffer(BUF_SERIAL1, ch);
                }
            } else if ((ch >= 32) && (ch <= 126)) {
                if (inputBuffers[BUF_SERIAL1].length == INPUT_BUFFER_LENGTH) {
                    resetInputBuffer(BUF_SERIAL1);
                } else {
                    appendInputBuffer(BUF_SERIAL1, ch);
                }
            }
        }
    }
    return false;
}

void resetInputBuffer(int buf) {
    inputBuffers[buf].data[0] = '\0';
    inputBuffers[buf].length = 0;
}

void appendInputBuffer(int buf, char ch) {
    inputBuffers[buf].data[inputBuffers[buf].length++] = ch;
    inputBuffers[buf].data[inputBuffers[buf].length] = '\0';
}

void enablePumps() {
    digitalWriteFast(PIN_ENABLE, LOW);
    turnOnLED();
    pumpsEnabled = true;
}

void disablePumps() {
    digitalWriteFast(PIN_ENABLE, HIGH);
    turnOffLED();
    pumpsEnabled = false;
}

void turnOnLED() {
    digitalWriteFast(PIN_LED, HIGH);
    ledOn = true;
}

void turnOffLED() {
    digitalWriteFast(PIN_LED, LOW);
    ledOn = false;
}

void toggleLED() {
    if (ledOn) turnOffLED();
    else turnOnLED();
}

void setPumpSpeed(int speed) {
    for (byte i = 0; i < PUMPS; i++) {
        allPumps[i]->setMaxSpeed(speed);
        allPumps[i]->setAcceleration(pumpAccel);
        pumpControllers[i] = NULL;
    }
}

void processCommand() {
    char* cmd = inputBuffers[BUF_SERIAL].data;
    int len = inputBuffers[BUF_SERIAL].length;
    
    switch (cmd[0]) {
        case 'C':
            if (! processChecksum(cmd, len)) break;
        case 'c':
            processCommCommand(cmd + 1);
            break;
        case 'P':
            if (! processChecksum(cmd, len)) break;
        case 'p':
            processPumpCommand(cmd + 1);
            break;
        default:
            if (commEnabled && serialSpeed) {
                strcpy(lastSerial1Command, inputBuffers[BUF_SERIAL].data);
                Serial1.println(lastSerial1Command);
                checksumRetries = 0;
            } else
                sendError("invalid command");
            break;
    }
}

bool processChecksum(char* cmd, int len) {
    if ((len <= 3) || (cmd[len - 3] != '~')) {
        sendError("CHK");
        return false;
    }
    char* hex = cmd + len - 2;
    len -= 3;
    cmd[len] = '\0';
    uint8_t sentCS = readHex(&hex);
    uint8_t calcCS = 0;
    for (int i = 0; i < len; i++)
        calcCS ^= cmd[i];
    if (sentCS != calcCS) {
        sendError("CHK");
        return false;
    }
    return true;
}

// =========== Comm commands
void processCommCommand(char* cmd) {
    switch (cmd[0]) {
        case 'E':
        case 'e':
            cmdCommEnable();
            return;
        case 'D':
        case 'd':
            if (detectSerial1Speed())
                cmdCommStatus();
            else
                sendError("unable to detect serial speed");
            return;
        case 'P':
        case 'p':
            if (ping())
                sendOK();
            else
                sendError("timeout");
            break;
        case 'S':
        case 's':
            cmdCommSpeed(cmd + 1);
            break;
        case '?':
            cmdCommStatus();
            break;
        default:
            sendError("invalid comm command");
            break;
    }
}

void cmdCommEnable() {
    if (commEnabled)
        commEnabled = false;
    else
        commEnabled = true;
    sendOK();
}

void cmdCommSpeed(char* str) {
    uint32_t speed = readUInt(&str);
    if (speed == 0)
        serialSpeed = 0;
    else {
        serialSpeed = speed;
        Serial1.begin(speed, SERIAL_8N1);
    }
    sendOK();
}

void cmdCommStatus() {
    send("enabled: ");
    sendInt(commEnabled);
    sendChar('\n');
    
    send("speed: ");
    sendInt(serialSpeed);
    sendChar('\n');
    
    sendOK();
}

// =========== Pump commands

void processPumpCommand(char* cmd) {
    switch (cmd[0]) {
        case 'P':
        case 'p':
            cmdPumpPump(cmd + 1);
            break;
        case 'H':
        case 'h':
            cmdPumpHalt(cmd + 1);
            break;
        case 'F':
        case 'f':
            cmdPumpFlush(cmd + 1);
            break;
        case 'S':
        case 's':
            cmdPumpSpeed(cmd + 1);
            break;
        case 'A':
        case 'a':
            cmdPumpAcceleration(cmd + 1);
            break;
        case 'E':
        case 'e':
            cmdPumpToggleEnable(cmd + 1);
            break;
        case '?':
            cmdPumpStatus();
            break;
        default:
            sendError("invalid pump command");
            break;
    }
}

/*
PP<#>,<[-]steps>,<speed>,<accel>
*/
void cmdPumpPump(char* str) {
    
    if (pumpsFlushing) {
        sendError("pumps are flushing");
        return;
    }
    
    byte pumpNum;
    if (str[0] == '?') {
        // debugging stuff to allow ? as pump num to mean next unused pump
        pumpNum = PUMPS + 1;
        for (byte i = 0; i < PUMPS; i++) {
            if (! pumpControllers[i]) {
                pumpNum = i;
                break;
            }
        }
        str++;
    } else {
        pumpNum = readUInt(&str);
    }
    readDelim(&str);
    
    if (pumpNum >= PUMPS) {
        sendError("invalid pump");
        return;
    }
    if (pumpControllers[pumpNum]) {
        sendError("pump is running");
        return;
    }
    
    int steps = readInt(&str);
    readDelim(&str);
    if (steps == 0) {
        sendError("invalid steps");
        return;
    }
    int dir = steps < 0 ? -1 : 1;
    
    if ((pumpDir != 0) && (dir != pumpDir)) {
        sendError("invalid direction");
        return;
    }
    
    int speed = readUInt(&str);
    readDelim(&str);
    if (speed == 0) speed = pumpSpeed;
    
    int accel = readUInt(&str);
    readDelim(&str);
    if (accel == 0) accel = pumpAccel;
    
    // find an unused controller
    StepControl<>* ctrl = NULL;
    for (byte i = 0; i < PUMP_CONTROLLERS; i++) {
        if (! allPumpControllers[i]->isRunning()) {
            ctrl = allPumpControllers[i];
            break;
        }
    }
    if (ctrl == NULL) {
        sendError("too busy");
        return;
    }
    
    enablePumps();
    allPumps[pumpNum]->setPosition(0);
    allPumps[pumpNum]->setAcceleration(accel);
    pumpControllers[pumpNum] = ctrl;
    pumpDir = dir;

    if ((steps == 1) || (steps == -1)) {
        allPumps[pumpNum]->setMaxSpeed(speed * dir);
        ctrl->rotateAsync(*allPumps[pumpNum]);
    } else {
        allPumps[pumpNum]->setMaxSpeed(speed);
        allPumps[pumpNum]->setTargetAbs(steps);
        ctrl->moveAsync(*allPumps[pumpNum]);
    }
    
    sendOK();
    sendPumpRunning(pumpNum);
}

void cmdPumpHalt(char* str) {
    
    if (pumpsFlushing) {
        sendError("pumps are flushing");
        return;
    }
    
    byte pumpNum;
    pumpNum = readInt(&str);
    
    if (pumpNum >= PUMPS) {
        sendError("invalid pump");
        return;
    }
    if (pumpControllers[pumpNum]) {
        pumpControllers[pumpNum]->stopAsync();
    }
    sendOK();
}

void cmdPumpFlush(char* str) {
    if (str[0] == 0) {
        // stop flushing
        if (pumpsFlushing) {
            pumpCtrl0.stopAsync();
        }
        sendOK();
            
    } else {
        // start flushing
        if (pumpsFlushing) {
            sendError("pumps are already flushing");
            return;
        }
        if (pumpsAreRunning()) {
            sendError("pumps are running");
            return;
        }
        
        Stepper* pumps[PUMPS] = {NULL};
        
        for (int i = 0; i < PUMPS; i++) {
            unsigned p = readUInt(&str);
            if (p >= PUMPS) {
                sendError("invalid pump");
                return;
            }
            pumps[i] = allPumps[p];
            pumps[i]->setPosition(0);
            pumps[i]->setAcceleration(pumpAccel);
            pumps[i]->setMaxSpeed(pumpSpeed);
            pumpControllers[p] = &pumpCtrl0;
            sendPumpRunning(p);
            
            if (! readDelim(&str)) break;
        }
        
        enablePumps();
        pumpCtrl0.rotateAsync(pumps);
        
        pumpsFlushing = true;
        sendOK();
    }
}

void cmdPumpSpeed(char* str) {
    int speed = readInt(&str);
    if ((speed < PUMP_MIN_SPEED) || (speed > PUMP_MAX_SPEED)) {
        sendError("invalid speed");
        return;
    }
    pumpSpeed = speed;
    sendOK();
}

void cmdPumpAcceleration(char* str) {
    unsigned accel = readUInt(&str);
    if ((accel < PUMP_MIN_ACCEL) || (accel > PUMP_MAX_ACCEL)) {
        sendError("invalid acceleration");
        return;
    }
    pumpAccel = accel;
    sendOK();
}

void cmdPumpToggleEnable(char* str) {
    if (pumpsEnabled) {
        pumpsEnabledOverride = false;
        sendMessage("disabled");
    } else {
        enablePumps();
        pumpsEnabledOverride = true;
        sendMessage("enabled");
    }
    sendOK();
}

void cmdPumpStatus() {
    send("enable override: ");
    sendInt(pumpsEnabledOverride);
    sendChar('\n');
    
    send("speed: ");
    sendInt(pumpSpeed);
    sendChar('\n');
    
    send("acceleration: ");
    sendInt(pumpAccel);
    sendChar('\n');
    
    for (byte i = 0; i < PUMPS; i++) {
        sendChar('P');
        sendInt(i);
        send(": ");
        if (pumpControllers[i]) send("running");
        sendChar('\n');
    }
    
    for (byte i = 0; i < PUMP_CONTROLLERS; i++) {
        send("PC");
        sendInt(i);
        send(": ");
        if (allPumpControllers[i]->isOk()) send("OK");
        else send("ERR");
        if (allPumpControllers[i]->isRunning()) send(",running");
        sendChar('\n');
    }
    
    sendOK();
}

// =========== Other stuff

int readInt(char** strPtr) {
    bool neg = false;
    int i = 0;
    char* str = *strPtr;
    if (*str == '-') {
        str++;
        neg = true;
    }
    while ((*str >= '0') && (*str <= '9')) {
        i = (i * 10) + (*str - '0');
        str++;
    }
    *strPtr = str;
    return neg ? -i : i;
}

unsigned readUInt(char** strPtr) {
    unsigned i = 0;
    char* str = *strPtr;
    while ((*str >= '0') && (*str <= '9')) {
        i = (i * 10) + (*str - '0');
        str++;
    }
    *strPtr = str;
    return i;
}

unsigned readHex(char** strPtr) {
    unsigned i = 0;
    char* str = *strPtr;
    while (1) {
        if ((*str >= '0') && (*str <= '9')) {
            i = (i << 4) + (*str - '0');
            str++;
        } else if ((*str >= 'a') && (*str <= 'f')) {
            i = (i << 4) + (*str - 'a') + 10;
            str++;
        } else if ((*str >= 'A') && (*str <= 'F')) {
            i = (i << 4) + (*str - 'A') + 10;
            str++;
        } else
            break;
    }
    *strPtr = str;
    return i;
}

bool readDelim(char** strPtr) {
    return readDelim(strPtr, ',');
}

bool readDelim(char** strPtr, char delim) {
    char* str = *strPtr;
    if (*str == delim) {
        str++;
        *strPtr = str;
        return true;
    } else {
        return false;
    }
}

void send(const char* str) {
    Serial.print(str);
}

void sendChar(char ch) {
    Serial.print(ch);
}

void sendInt(int32_t i) {
    Serial.print(i);
}

void sendOK() {
    send("OK\n");
}

void sendError(const char* msg) {
    sendChar('!');
    send(msg);
    sendChar('\n');
}

void sendMessage(const char* msg) {
    sendChar('#');
    send(msg);
    sendChar('\n');
}

void sendPumpRunning(byte pumpNum) {
    send("*PR");
    sendInt(pumpNum);
    sendChar('\n');
}

void sendPumpStopped(byte pumpNum) {
    send("*PS");
    sendInt(pumpNum);
    sendChar(',');
    sendInt(allPumps[pumpNum]->getPosition());
    sendChar('\n');
}

bool pumpsAreRunning() {
    return pumpCtrl0.isRunning() ||
           pumpCtrl1.isRunning() ||
           pumpCtrl2.isRunning() ||
           pumpCtrl3.isRunning();
}

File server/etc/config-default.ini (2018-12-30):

[db]
dbFile: var/barbot.db

[logging]
console: false
logLevel: INFO
logFile: var/barbot.log
logFormat: %(asctime)s [%(threadName)s] [%(name)s] [%(levelname)s]: %(message)s
logSize: 1000000
logCount: 3
level.socketio = WARNING
level.engineio = WARNING
level.werkzeug = WARNING

[server]
pidFile: var/barbot.pid
binDir: bin
contentDir: ../client/dist
listenAddress: 0.0.0.0
listenPort: 8080
socketIODebug: false
configCheckInterval: 2

[core]
diskFreeCommand: df --output=pcent {}
diskFreePath: var
restartCommand: sudo shutdown -r now
shutdownCommand: sudo shutdown -h now
restartXCommand: sudo systemctl restart display-manager
restartDelay: 5
shutdownDelay: 5
shutdownTimer: 20

[dispenser]
maxDrinkOrderAge: 3600
favoriteDrinkCount: 20
drinkOrderCheckInterval: 5
idleAudioInterval: 60
idleAudioChance: 0.3

[wifi]
interface: wlan0
checkInterval: 10
wpaSupplicantFile: /etc/wpa_supplicant/wpa_supplicant.conf

[serial]
port: /dev/ttyACM0
speed: 115200

[settings]
settingsFile: var/settings.ini
settingsCheckInterval: 5

appTitle: Barbot
autoConsole: true
isConsole: false
restartRequiresAdmin: false
restartXRequiresAdmin: false
shutdownRequiresAdmin: false
settingsRequiresAdmin: false
dispenserSetupRequiresAdmin: false
enableIdleAudio: true
enableLocalAudio: true
enableRemoteAudio: true
drinkSizeLimit: 475
parentalCode:
volume: 1.0

[lights]
enabled: true
startupPattern:                 1:2:3:4,0,2,60:60:60,0,20,7
shutdownPattern:                1:2:3:4,0,2,60:60:60,0,20,7
restartPattern:                 1:2:3:4,0,2,60:60:60,0,20,7
idlePattern:                    1:2:3:4,0,1,60:60:60,20,3

waitForDispensePattern:         1:2:3:4,0,2,0:0:60,0,20,7
startDispensePattern:           0,2,5,0
glassRemovedDispensePattern:    1:2:3:4,0,2,60:0:0,0,10,7
endDispensePattern:             1:2:3:4,0,1,0:60:0,10,3

manualDispenseIdlePattern:      1:2:3:4,0,1,60:60:60,10,3
manualDispensePattern:          0,2,5,0

setupDispenseIdlePattern:       1:2:3:4,0,1,60:60:60,10,3
setupDispensePattern:           0,2,5,0

#idlePattern:
#waitForDispensePattern:
#startDispensePattern:
#glassRemovedDispensePattern:
#endDispensePattern:

#manualDispenseIdlePattern:
#manualDispensePattern:

#setupDispenseIdlePattern:
#setupDispensePattern:


[units]
default: oz
order: oz,ml,l,qt,tsp,tbsp
# name: ml,precision
oz: 29.5735,1
ml: 1,1
l: 1000,3
qt: 946.353,3
tsp: 4.93,1
tbsp: 14.787,1

[audio]
enabled: true
audioDir: audio
fileCheckInterval: 5
purgeClips: true
inProcessTTS: false
clipFormat: mp3

[pumps]
count: 16
primeFactor: 1.0
cleanFactor: 1.1
drainFactor: 1.1
stepsPerML: 1582
speed: 12000
acceleration: 7500
ingredientEmptyAmount: 10
limitRunTime: 60
1: 17
2: 19.3
3: 18.2
4: 19
5: 18.2
6: 21.8
7: 22.4
8: 22
9: 17.9
10: 18.6
11: 17.7
12: 19.5
13: 18.4
14: 20.8
15: 21.5
16: 22.4

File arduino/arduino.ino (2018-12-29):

/*
Copyright 2018 Thomas A. Bennedum

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
THE SOFTWARE IS PROVIDED "AS IS", WITHOUT WARRANTY OF ANY KIND, EXPRESS OR
IMPLIED, INCLUDING BUT NOT LIMITED TO THE WARRANTIES OF MERCHANTABILITY,
FITNESS FOR A PARTICULAR PURPOSE AND NONINFRINGEMENT. IN NO EVENT SHALL
THE AUTHORS OR COPYRIGHT HOLDERS BE LIABLE FOR ANY CLAIM, DAMAGES OR OTHER
LIABILITY, WHETHER IN AN ACTION OF CONTRACT, TORT OR OTHERWISE, ARISING
FROM, OUT OF OR IN CONNECTION WITH THE SOFTWARE OR THE USE OR OTHER DEALINGS
IN THE SOFTWARE.
*/

/*
    https://github.com/adafruit/Adafruit_NeoPixel
    https://github.com/frdfsnlght/NeoPixel-Patterns
*/


#include <Arduino.h>
#include <EEPROM.h>
#include <NeoPixelController.h>
#include <MultiWipeNeoPixelPattern.h>
#include <BlinkNeoPixelPattern.h>
#include <RainbowNeoPixelPattern.h>
#include <ChaseNeoPixelPattern.h>
#include <ScanNeoPixelPattern.h>
#include <FadeNeoPixelPattern.h>
#include <Colors.h>

//#define DEBUG_PATTERNS

constexpr unsigned long SERIAL_SPEED    = 115200;

constexpr int PIN_SERIAL_RX             = 0;
constexpr int PIN_SERIAL_TX             = 1;

constexpr int PIN_LIGHTS                = 2;
constexpr int PIN_SENSOR0               = 3;
constexpr int PIN_SENSOR1               = 4;
constexpr int PIN_RELAY0                = 5;
constexpr int PIN_RELAY1                = 6;
constexpr int PIN_RELAY2                = 7;
constexpr int PIN_BUTTON                = 8;
constexpr int PIN_LED                   = 13;


constexpr int NUM_PIXELS_PER_SUBSEGMENT = 13;
constexpr int NUM_SUBSEGMENTS           = 4;
constexpr int NUM_SEGMENTS              = NUM_SUBSEGMENTS + 1;
constexpr int NUM_PIXELS                = NUM_PIXELS_PER_SUBSEGMENT * NUM_SUBSEGMENTS;
constexpr int NUM_PATTERN_SLOTS         = 8;
constexpr int PATTERN_SLOT_BASE         = 0;
constexpr int NUM_SENSORS               = 2;
constexpr int SENSOR_PINS[]             = {PIN_SENSOR0, PIN_SENSOR1};

constexpr int INPUT_BUFFER_LENGTH       = 64;

constexpr unsigned long LED_TOGGLE_INTERVAL_FAST    = 250;
constexpr unsigned long LED_TOGGLE_INTERVAL_SLOW    = 1000;
constexpr unsigned long SENSOR_READ_INTERVAL        = 250;
constexpr unsigned long BUTTON_PRESS_SHORT          = 1000;
constexpr unsigned long BUTTON_PRESS_LONG           = 8000;
constexpr unsigned long RELAY1_ON_DELAY             = 1000;
constexpr unsigned long RELAY2_ON_DELAY             = 0;
constexpr int POWERDOWNTIME_DISABLED                = -1;

constexpr byte PATTERN_MULTIWIPE        = 0;
constexpr byte PATTERN_BLINK            = 1;
constexpr byte PATTERN_RAINBOW          = 2;
constexpr byte PATTERN_CHASE            = 3;
constexpr byte PATTERN_SCAN             = 4;
constexpr byte PATTERN_FADE             = 5;

constexpr byte STATE_OFF                = 0;
constexpr byte STATE_OFF_P              = 1;
constexpr byte STATE_OFF_LP             = 2;
constexpr byte STATE_WAIT_ON            = 3;
constexpr byte STATE_WAIT_ON_SP         = 4;
constexpr byte STATE_ON                 = 5;
constexpr byte STATE_ON_P               = 6;
constexpr byte STATE_ON_SP              = 7;

constexpr int ERR_OK                    = 0;
constexpr int ERR_NO_PATTERN            = 1;
constexpr int ERR_INVALID_PATTERN       = 2;



typedef struct {
    char data[INPUT_BUFFER_LENGTH];
    uint16_t length;
} inputBuffer_t;
    
inputBuffer_t inputBuffer;
int ch;

// Parameter 1 = number of pixels in strip
// Parameter 2 = number of segments in the strip
// Parameter 3 = pin number
// Parameter 4 = pixel type flags, add together as needed:
//   NEO_KHZ800  800 KHz bitstream (most NeoPixel products w/WS2812 LEDs)
//   NEO_KHZ400  400 KHz (classic 'v1' (not v2) FLORA pixels, WS2811 drivers)
//   NEO_GRB     Pixels are wired for GRB bitstream (most NeoPixel products)
//   NEO_RGB     Pixels are wired for RGB bitstream (v1 FLORA pixels, not v2)
//   NEO_RGBW    Pixels are wired for RGBW bitstream (NeoPixel RGBW products)
NeoPixelController lights = NeoPixelController(NUM_PIXELS, NUM_SEGMENTS, PIN_LIGHTS, NEO_GRB + NEO_KHZ800);
uint8_t segments = 0;

// onComplete callback function
//void lightPatternComplete(NeoPatterns * aLedsPtr);

// IMPORTANT: To reduce NeoPixel burnout risk, add 1000 uF capacitor across
// pixel power leads, add 300 - 500 Ohm resistor on first pixel's data input
// and minimize distance between controller and first pixel.  Avoid connecting
// on a live circuit...if you must, connect GND first.

MultiWipeNeoPixelPattern multiWipePatterns[NUM_SEGMENTS] = {};
BlinkNeoPixelPattern blinkPatterns[NUM_SEGMENTS] = {};
RainbowNeoPixelPattern rainbowPatterns[NUM_SEGMENTS] = {};
ChaseNeoPixelPattern chasePatterns[NUM_SEGMENTS] = {};
ScanNeoPixelPattern scanPatterns[NUM_SEGMENTS] = {};
FadeNeoPixelPattern fadePatterns[NUM_SEGMENTS] = {};


bool sensors[NUM_SENSORS];
uint32_t lastSensorReadTime = 0;

bool ledOn = false;
uint32_t lastLEDToggleTime = 0;

int powerDownTime = POWERDOWNTIME_DISABLED;
uint32_t lastPowerDownTickTime = 0;

uint8_t state = STATE_OFF;
uint32_t buttonPressedTime = 0;


void setup() {
    Serial.begin(SERIAL_SPEED, SERIAL_8N1);

    pinMode(PIN_RELAY0, OUTPUT);
    pinMode(PIN_RELAY1, OUTPUT);
    pinMode(PIN_RELAY2, OUTPUT);
    
    for (int i = 0; i < NUM_SENSORS; i++) {
        sensors[i] = false;
        pinMode(SENSOR_PINS[i], INPUT);
        digitalWrite(SENSOR_PINS[i], HIGH); // enable pullup
    }
    
    pinMode(PIN_BUTTON, INPUT);
    digitalWrite(PIN_BUTTON, HIGH); // enable pullup
    
    pinMode(PIN_LED, OUTPUT);
    
    turnOffRelays();
    
    lights.setupSegment(0, 0, NUM_PIXELS);
    for (int i = 0; i < NUM_SUBSEGMENTS; i++) {
        lights.setupSegment(i + 1, i * NUM_PIXELS_PER_SUBSEGMENT, NUM_PIXELS_PER_SUBSEGMENT);
    }
    lights.begin();
    lights.setSegmentColor(COLOR_OFF, 0);
    
    turnOffLED();
        
    sendMessage(F("Barbot-Arduino ready"));
}

void loop() {
    loopSerial();
    loopLights();
    loopButton();
    loopSensor();
    loopPower();
    loopLED();
}
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

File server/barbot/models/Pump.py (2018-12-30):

import logging, time, threading, re
from peewee import *
from threading import Lock, Timer

from ..db import db, BarbotModel, ModelError, addModel
from ..config import config
from ..bus import bus
from .. import units
from .. import serial
from .Ingredient import Ingredient


_pumpRunEventPattern = re.compile(r"(?i)PR(\d+)")
_pumpStopEventPattern = re.compile(r"(?i)PS(\d+),(-?\d+)")

_logger = logging.getLogger('Models.Pump')

_pumpExtras = {}

@bus.on('server/start')
def _bus_serverStart():
    _bus_configLoaded()
    pumps = Pump.select()
    if len(pumps) != config.getint('pumps', 'count'):
        _logger.warning('Database pump count doesn\'t match configuration count!')
        Pump.delete().execute()
        for i in range(0, config.getint('pumps', 'count')):
            p = Pump()
            p.id = i + 1
            p.save(force_insert = True)
        _logger.info('Initialized pumps')

@bus.on('config/loaded')
def _bus_configLoaded():
    try:
        serial.write('PS{}'.format(config.getint('pumps', 'speed')), timeout = 1)
        serial.write('PA{}'.format(config.getint('pumps', 'acceleration')), timeout = 1)
    except serial.SerialError as e:
        _logger.error(e)
        
@bus.on('serial/event')
def _bus_serialEvent(e):
    from .Drink import Drink
    from .. import dispenser
    
    m = _pumpRunEventPattern.match(e)
    if m:
        pump = Pump.get_or_none(Pump.id == int(m.group(1)) + 1)
        if pump:
            with pump.lock:
                _logger.info('Pump {} running'.format(pump.name()))
                if not pump.running:
                    pump.running = True
                    bus.emit('model/pump/saved', pump)
                    
        return
        
    m = _pumpStopEventPattern.match(e)
    if m:
        pump = Pump.get_or_none(Pump.id == int(m.group(1)) + 1)
        if pump:
            with pump.lock:
                pump.running = False
                if pump.timer:
                    pump.timer.cancel()
                    pump.timer = None
                steps = int(m.group(2))
                pump.lastAmount = float(steps) / config.getfloat('pumps', 'stepsPerML')
                _logger.info('Pump {} stopped, {:.2f} mL ({} steps)'.format(pump.name(), pump.lastAmount, steps))
                
                rebuildMenu = False
                
                if pump.lastAmount > 0: # forward
                
                    if pump.isLoaded(): # primed
                        pump.setState(Pump.READY)
                        bus.emit('model/ingredient/saved', pump.ingredient)
                        rebuildMenu = True
                        
                    elif pump.isReady():
                        pump.amount = units.toOther(units.toML(pump.amount, pump.units) - pump.lastAmount, pump.units)
                        if pump.amount < 0:
                            pump.amount = 0
                        if units.toML(pump.amount, pump.units) < config.getint('pumps', 'ingredientEmptyAmount'):
                            pump.setState(Pump.EMPTY)
                            rebuildMenu = True
                            bus.emit('audio/play', 'pumpEmpty', console = True)
                        
                        ingredient = pump.ingredient
                        ingredient.timesDispensed = ingredient.timesDispensed + 1
                        ingredient.amountDispensed = ingredient.amountDispensed + pump.lastAmount
                        ingredient.save()
                        
                    elif pump.isDirty():
                        pump.setState(Pump.UNUSED)
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

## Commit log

2018-10-23 Added schematics and 3D directories
    [Enclosure.skp, Pump.skp, main.kicad_pcb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]
2018-10-24 PCBs started!
    [main.kicad_pcb, main.sch, module.sch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]
2018-10-25 Tuning and bug fixing.
    [DrinkOrder.py, Ingredient.py, audio.py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]
2018-10-25 Changed pin assignments
2018-10-25 Fixed sensor sense
2018-10-26 Fixed bad thrown exception
    [audio.py]
2018-10-26 Finished board designs.
    [main.kicad_pcb, main.sch, module.sch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]
2018-10-26 Fixed restart and shutdown process.
    [core.py]
2018-10-26 Added controller
    [Enclosure.skp]
2018-10-27 Tweak relay delay, added light pattern debugging
2018-10-29 Tweaked schematic and board
    [main.kicad_pcb, main.sch]
2018-10-29 Tweaked sun gears and roller for standard stepper
    [Pump.skp]
2018-10-29 More detail
    [Enclosure.skp]
2018-10-30 Tweaked some pads
    [main.kicad_pcb]
2018-10-31 Small tweaks
    [main.kicad_pcb, pump.kicad_pcb]
2018-10-31 Lots more work done
    [Enclosure.skp]
2018-11-01 Ignore existing PID file on startup.
2018-11-01 Added nut recess to dispenser head.
    [Enclosure.skp]
2018-11-01 Added STLs and print settings
    [Dispenser Head Part A.stl, Dispenser Head Part B.stl, Dispenser Head Part C.stl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]
2018-11-02 More printing
2018-11-02 More STLs
    [Clamp Block Left.stl, Clamp Block Right.stl, Planet Gear.stl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]
2018-11-02 Better serial command handling
    [Enclosure.skp]
2018-11-06 BOM and added panel
    [Enclosure.skp]
2018-11-08 Fixed audio effects bug
    [audio.py]
2018-11-08 New controller box
    [Enclosure.skp]
2018-11-09 New speakers and controller enclosure
    [Enclosure.skp]
2018-11-09 More controller design
    [Enclosure.skp]
2018-11-09 DB updates, audio fixes, volume control fixes, better daemon support
    [audio.py, config-default.ini, daemon.py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]
2018-11-13 Dimensioning for fabrication
    [Enclosure.skp]
2018-11-13 Reformatted BOM
2018-11-13 New STL
    [Speaker Grill.stl]
2018-11-13 New grill
    [Speaker Grill.stl]
2018-11-13 New design
    [Speaker Grill.stl]
2018-11-13 More STLs and 3D tuning
    [Drip Tray.stl, Enclosure.skp, Touchscreen Bracket.stl]
2018-11-13 Added pump flushing
2018-11-14 Updated URLs
    [Foo.stl]
2018-11-14 Refactored pump setup
2018-11-14 More STLs and enclosure tweaks
    [Enclosure.skp, Fan Grill.stl, Raspberry Pi Offset Bracket.stl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]
2018-11-20 Tweaks, new dispenser head part B
    [Dispenser Head Part B.stl, Enclosure.skp, Tubing Bender.stl]
2018-11-20 Redesigned dispenser tubing
    [Enclosure.skp]
2018-11-26 No real changes
    [main.sch, module.sch, pump.sch]
2018-11-26 Added position output on motor stop
2018-11-27 Bug fixes, some icons, cleanup
    [Pump.py, dispenser.py, serial.py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]
2018-11-28 Added simulated power button
2018-11-28 Finished Make My Own, componentized shit, bug fixes, more refactoring, etc.
    [Pump.py, config-default.ini, core.py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]
2018-11-29 Fixed checksum and socket bugs
    [arduino.ino, teensy.ino]
2018-11-30 Hopefully fixed comms between controllers
    [arduino.ino, teensy.ino]
2018-11-30 Set pump speed/accel on start
2018-12-03 Replaced utils with more configurable units
    [Drink.py, Pump.py, config-default.ini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]
2018-12-03 Fixed some units things
    [units.py]
2018-12-12 Added About screen, fixed scrollbars, cleaned up dialogs and events
    [dispenser.py, socket.py, wifi.py]
2018-12-12 Fixed bad event name
    [socket.py]
2018-12-14 Fixed a couple of bugs
2018-12-16 Added pumpEmpty audio clip
2018-12-16 Fixed continuous rotation forward/reverse
    [teensy.ino]
2018-12-16 Better pump values and playing with lights
2018-12-16 Fixed state transition for unloading pump
    [Pump.py]
2018-12-16 Disabled some light patterns until power down issue is resolved
    [config-default.ini]
2018-12-26 Replaced dynamic allocations with static, removed unused light patterns, renumbered existing patterns
    [arduino.ino]
2018-12-28 Fixed bus event name
    [logging.py]
2018-12-28 Fixed state transition to same state
    [Pump.py]
2018-12-29 Removed lights off on power up
2019-01-04 Fixed bad response key
    [socket.py]
